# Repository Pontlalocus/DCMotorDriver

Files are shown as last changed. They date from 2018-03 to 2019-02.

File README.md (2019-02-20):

# Project:  BJT HS DC Motor Driver

## DCMotorDriver
DC Motor Driver Simple Board using Bipolar Junction Transistor (BJT).

# 1.0  Glosary

**BJT** - Bipolar Junction Transistor

**DC** - Direct Current

**Qty**  - Quantity

**Mon** - Monitor

**PCB** - Printed Circuit Board

**Ref Des** - Reference Designator

## 2.0  Overview

DC Motor Driver board is a shield for Arduino nano to drive motors on the simplest way possible.   It uses only high side driver suply to the motor with Bipolar Junction Transistors (BJT).

The Board can handle 4 Motors each of the motors are connected to the V(+) and V(-) directly to the output.  No other connections to drive th motors are required.

This board will only operate as a high side driver with 4 oputputs that can handle PWM pulses.  The PWM pulses are internally generated on the Arduino nano.   It is important that the Arduino nano is assembled to the board and programmed with the correct software for the motors to be able to work.

The board is capable of reading the current of each motor independently by using a shunt resistor to ground.   The current measurement is injected to the Analaog port of the Arduino Nano.   We use the Ports A0 to A3 to each of the motor current.  More information on how to read the values is explained below.

## 3.0  Block Diagram

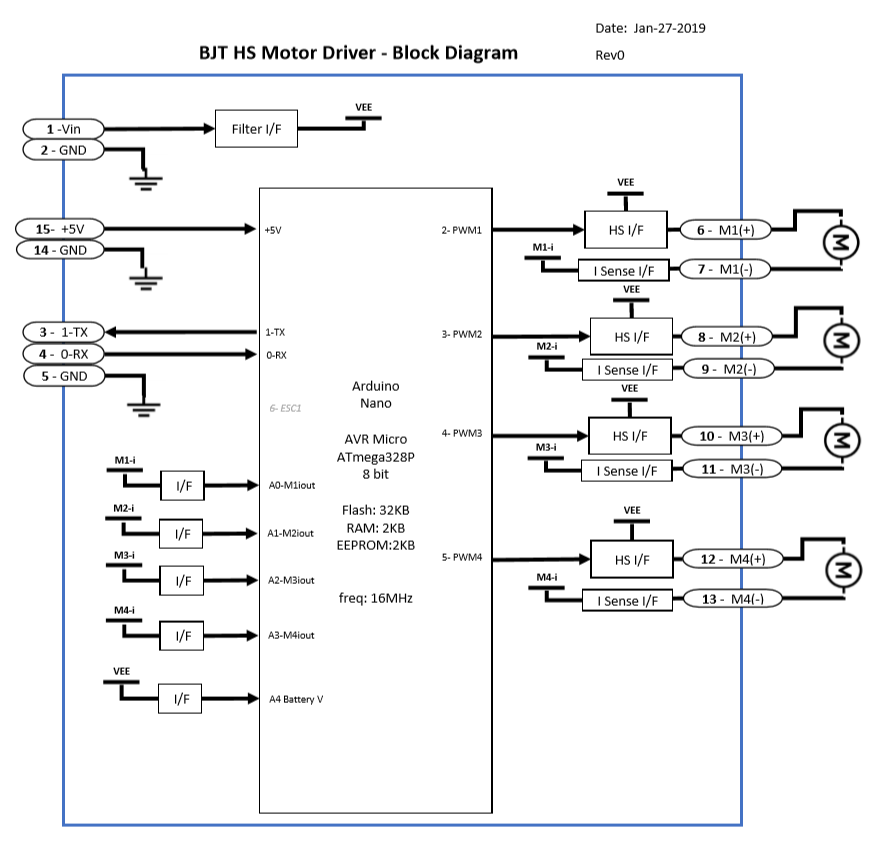
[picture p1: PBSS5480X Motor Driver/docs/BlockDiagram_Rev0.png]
BJT DC Motor Driver Block Diagram


## 4.0  External Connections   

## 4.1  Main Connector Pinout

|  Ref Des | Pin # | Signal Name | Description |
| --- |---| ---|---|
| P7 | 1 | Vin |  Power Battery |
| P7 | 2 | GND |  Ground |
| P7 | 3 | 1-TX |  Serial TX |
| P7 | 4 | 0-RX |  Serial RX |
| P7 | 5 | GND |  Ground |
| P7 | 6 | Motor1-V+ |  Motor1(+) |
| P7 | 7 | Motor1-V- |  Motor1(-) |
| P7 | 8 | Motor2-V+ |  Motor2(+) |
| P7 | 9 | Motor2-V- |  Motor2(-) |
| P7 | 10 | Motor3-V+ |  Motor3(+) |
| P7 | 11 | Motor3-V- |  Motor3(-) |
| P7 | 12 | Motor4-V+ |  Motor4(+) |
| P7 | 13 | Motor4-V- |  Motor4(-) |
| P7 | 14 | GND |  Ground |
| P7 | 15 | +5V |  Power +5V |

## 4.2  Arduino Nano Connector

|  Ref Des | Pin # | Signal Name | Description |
| --- |---| ---|---|
| P1 | 1 | 1-TX |  Serial TX |
| P1 | 2 | 0-RX |  Serial RX |
| P1 | 3 | Reset |  Reset |
| P1 | 4 | GND |  Ground |
| P1 | 5 | 2-PWM1 |  Motor1 - PWM1 |
| P1 | 6 | 3-PWM2 |  Motor2 - PWM2 |
| P1 | 7 | 4-PWM3 |  Motor3 - PWM3 |
| P1 | 8 | 5-PWM4 |  Motor4 - PWM4 |
| P1 | 9 | 6-ESC1 |  Reserved |
| P1 | 10 | Not Used |  Not Used |
| P1 | 11 | Not Used |  Not Used |
| P1 | 12 | Not Used |  Not Used |
| P1 | 13 | Not Used |  Not Used |
| P1 | 14 | Not Used |  Not Used |
| P1 | 15 | Not Used |  Not Used |
| P2 | 1 | Vin |  Power Battery |
| P2 | 2 | GND |  Ground |
| P2 | 3 | Reset |  Reset |
| P2 | 4 | +5V |  Power +5V |
| P2 | 5 | Not Used |  Not Used |
| P2 | 6 | Not Used |  Not Used |
| P2 | 7 | Not Used |  Not Used |
| P2 | 8 | A4 - Battery_V |  Battery Voltage IN |
| P2 | 9 | A3 - Motor4_iout | Motor 4 current Mon |
| P2 | 10 | A2 - Motor3_iout | Motor 3 current Mon |
| P2 | 11 | A1 - Motor2_iout | Motor 2 current Mon |
| P2 | 12 | A0 -  Motor2_iout| Motor 1 current Mon |
| P2 | 13 | AREF | Not Used |
| P2 | 14 | +3.3V | Power 3.3V |
| P2 | 15 | 13 - SCK | Serial Clock |

## 5.0  General Specifications

General Specifications include typical operation specifications

## 5.1  Typical Specifications

**Operation Voltage**: Battery Vin must be equal to 9V +/- 1V
**Operating Temperature**: 0°C to 40°C
**Battery Input Current**:
1.  No Load = <_Pending_>.
2.  Individual Motor Max Load =<_xx A_>.
3.  All Motors Max Load = <_xx A_>.

**Battery Voltage Monitor Range**:  VBAT * 0.5.

**Battery Monitor Low Pass Filter**: <_Pending_>.

**Motor Current Monitor Formula**: Current * 0.1 in Amps.

**Motor Current Low Pass Filter**: <_Pending_>.

_Note: Motor current is same formula for all motors: Motor1, Motor2, Motor3 and Motor4

##  Project Design

## 6.1  Schematic Diagram

Refer to Schematic Diagram for wiring connections of the Project

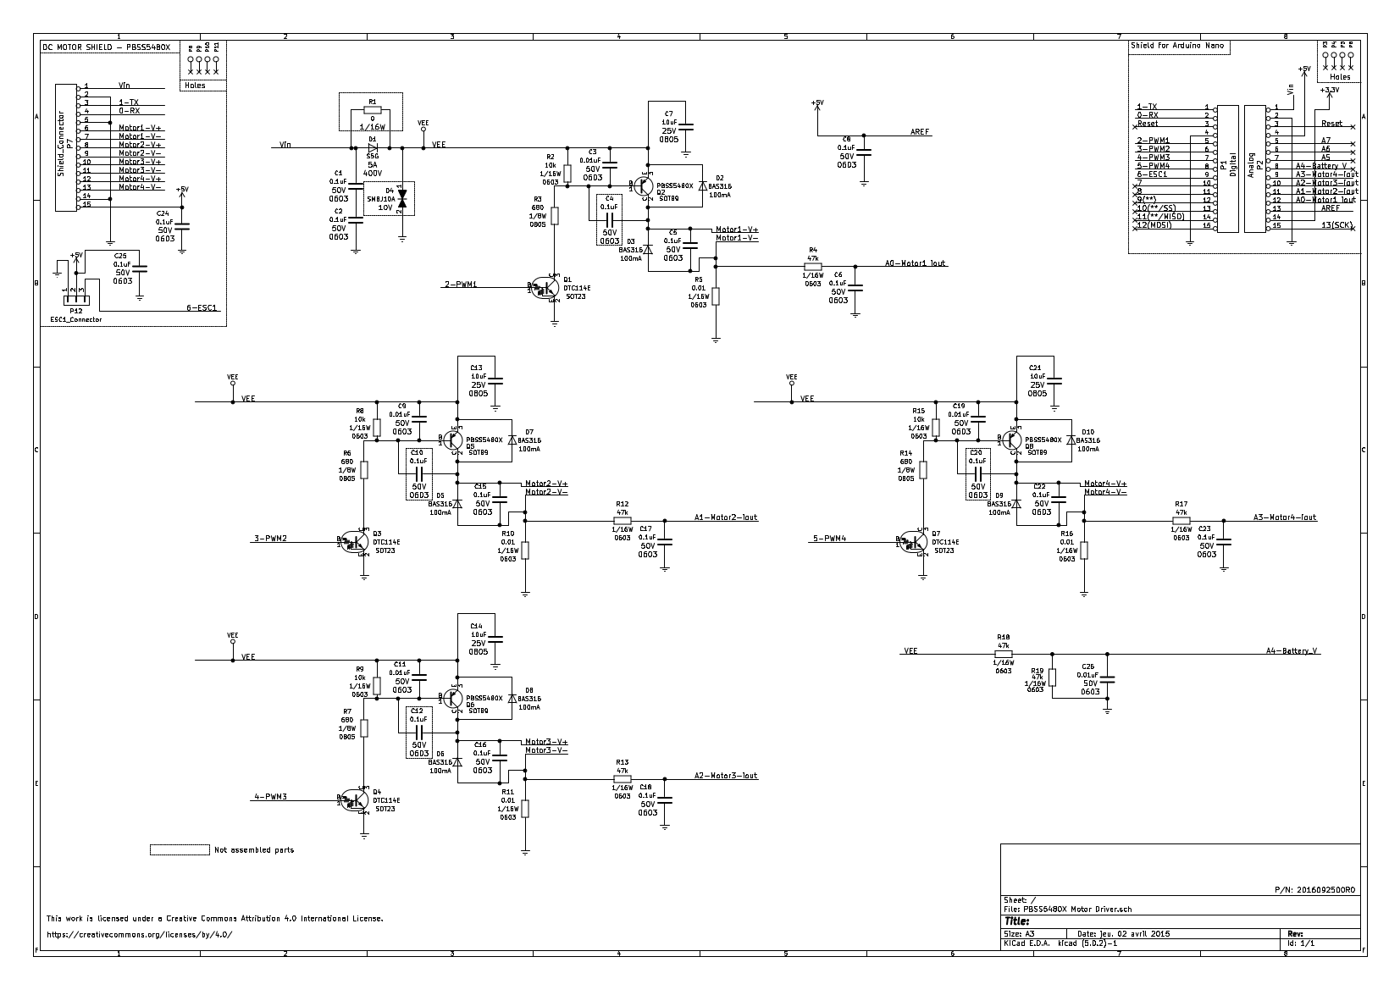
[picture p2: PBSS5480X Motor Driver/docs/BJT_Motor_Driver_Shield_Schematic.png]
Schematic Diagram


This project requires the Arduino Nano board to be used.  For information on the schematic diagram of the Arduino Nano please refer to the following page

Arduino Nano Schematic Diagram

Note: External Link

## 6.2 Bill of Material

The following list of components are selected for the Design.  All are discrete components:

|  Item # | Description | Qty | Reference Designator |
| --- |---| ----|---|
| 1 | PCB bare boards FR-4 Tg=140 2L | 1 |  PCB 1 |
| 2 | DIODE GEN PURP 250V 200MA SOD323 | 8 |  D2 D3 D7 D5 D8 D6 D9 D10 |
| 3 | CAP CER 10000PF 50V X7R 0603 | 5 |  C3 C9 C11 C19 C26 |
| 4 | CAP CER 0.1UF 50V X7R 0603 | 17  |  C6 C8 C17 C18 C23 C1 C2 C5 C15 C16 C22 C24 C25 |
| 5 | CAP CER 10UF 16V X7R 0805 | 4 |  C7 C13 C14 C21 |
| 6 | TRANS PNP 80V 4A SOT89 | 4 |  Q2 Q5 Q6 Q8 |
| 7 | TRANS PREBIAS NPN 246MW SOT23-3  | 4 |  Q1 Q3 Q4 Q7 |
| 8 | RES 0.01 OHM 1% 1/4W 0603 | 4 |  R5 R10 R11 R16 |
| 9 | RES SMD 10K OHM 5% 1/10W 0603 | 4 |  R2 R8 R9 R15 |
| 10 | RES SMD 47K OHM 5% 1/10W 0603 | 6 |  R4 R12 R13 R17 R18 R19 |
| 11 | RES SMD 0 OHM JUMPER 1/10W 0603  | 0 | |
| 12 | RES SMD 680 OHM 1% 1/8W 0805 | 4 |  R3 R6 R7 R14 |
| 13 | DIODE GEN PURP 400V 5A DO214AB | 1 |  D1 |
| 14 | TVS DIODE 10V 17V DO214AA | 1 |  D4 |
| 15 | Arduino Nano Board | 1 |  BOARD 1 |

The following list are components that are not assembled in the board

### Not Assembled 
C4 C10 C12 C20 R1

## 6.3  PCB Specification

PCB Board is FR-4.  Tickness 1.6mm.  2 layers.  Top Side Assembly.  Silkscreen in Top Side only.

Supplier selected for the first Job is JLPCB

### 6.3.1 PCB Design Top View 

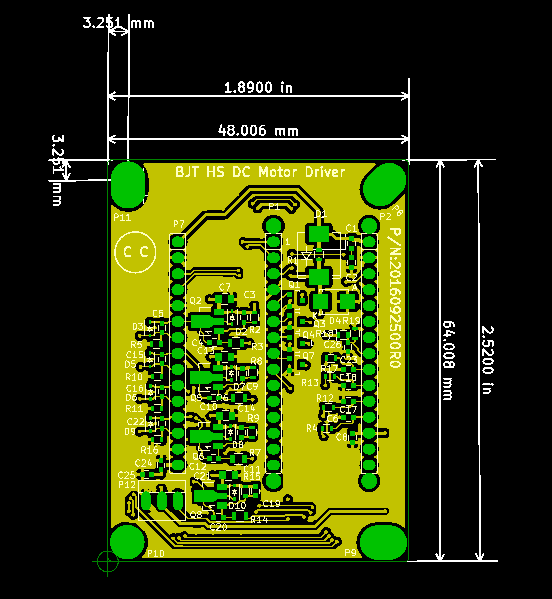
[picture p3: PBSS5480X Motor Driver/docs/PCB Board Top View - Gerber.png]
PCB Top View


### 6.3.2 PCB Design Bottom View

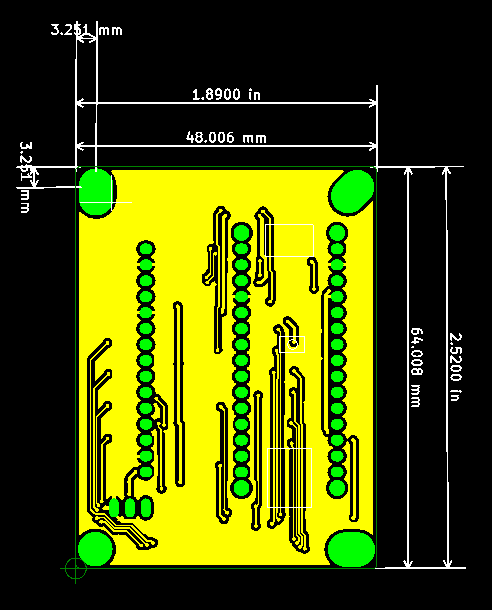
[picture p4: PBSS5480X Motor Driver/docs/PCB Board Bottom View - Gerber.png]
PCB Bottom View


##  7.0  Design Verification

For making sure the board functioanlity is working correctly the following Components are used.  Follow the connection diagram and test the functioanlity of the board with this Software

## 7.1  External Components Requirements

Required External Components

### 7.1.1  Power Pack

Power Pack: 9V
Example:
<_Pending_>.

### 7.1.2  DC Voltage Regulator

DC Voltage Regulator 5V
Example:
<_Pending_>.

### 7.1.3  DC Motor

2.  DC Motor: 
Example:
<_Pending_>.

## 7.2  Design Verification Connections

Todo:  Add connections to system with actual pictures

## 7.3  Design Verification Software

Todo:  Software components,  How does the software works, how to flash software,  how to run software, 

## 7.4  Measure of the output signals and confirmation of General Specifications

Todo:  use a measurement device to confirm General Specifications:  Supply Voltage, Actual current vs adruino measured x 4, PWM signal x 4, Battery Monitor. 

## 8.0  Future Generation Improvements

### 8.1 TODO
1.  Add MQTT RF Transmitter
2.  Add Sensors for 3 axis accelerometer, Gyroscpe and Compass
3.  Add Output for Servo

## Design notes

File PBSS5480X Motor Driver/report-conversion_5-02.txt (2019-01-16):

Info: Backing up file “C:\Users\eduar\OneDrive\Documents\Github\DCMotorDriver\PBSS5480X Motor Driver\sym-lib-table” to file “C:\Users\eduar\OneDrive\Documents\Github\DCMotorDriver\PBSS5480X Motor Driver\rescue-backup\sym-lib-table-2019-01-15-23-58-39”.
Info: Backing up file “C:\Users\eduar\OneDrive\Documents\Github\DCMotorDriver\PBSS5480X Motor Driver\PBSS5480X Motor Driver.sch” to file “C:\Users\eduar\OneDrive\Documents\Github\DCMotorDriver\PBSS5480X Motor Driver\rescue-backup\PBSS5480X Motor Driver-2019-01-15-23-58-39.sch”.
Info: Backing up file “C:\Users\eduar\OneDrive\Documents\Github\DCMotorDriver\PBSS5480X Motor Driver\PBSS5480X Motor Driver.pro” to file “C:\Users\eduar\OneDrive\Documents\Github\DCMotorDriver\PBSS5480X Motor Driver\rescue-backup\PBSS5480X Motor Driver-2019-01-15-23-58-39.pro”.
Info: Backing up file “C:\Users\eduar\OneDrive\Documents\Github\DCMotorDriver\PBSS5480X Motor Driver\PBSS5480X Motor Driver-cache.lib” to file “C:\Users\eduar\OneDrive\Documents\Github\DCMotorDriver\PBSS5480X Motor Driver\rescue-backup\PBSS5480X Motor Driver-cache-2019-01-15-23-58-39.lib”.
Info: Backing up file “C:\Users\eduar\OneDrive\Documents\Github\DCMotorDriver\PBSS5480X Motor Driver\PBSS5480X Motor Driver-rescue.lib” to file “C:\Users\eduar\OneDrive\Documents\Github\DCMotorDriver\PBSS5480X Motor Driver\rescue-backup\PBSS5480X Motor Driver-rescue-2019-01-15-23-58-39.lib”.
Info: Backing up file “C:\Users\eduar\OneDrive\Documents\Github\DCMotorDriver\PBSS5480X Motor Driver\PBSS5480X Motor Driver-rescue.dcm” to file “C:\Users\eduar\OneDrive\Documents\Github\DCMotorDriver\PBSS5480X Motor Driver\rescue-backup\PBSS5480X Motor Driver-rescue-2019-01-15-23-58-39.dcm”.
Info: Adding library “PBSS5480X-Motor-Driver-rescue”, file “${KIPRJMOD}/PBSS5480X Motor Driver-rescue.lib” to project symbol library table.
Symbol “CONN_1” mapped to symbol library “PBSS5480X-Motor-Driver-rescue”.
Symbol “CONN_1” mapped to symbol library “PBSS5480X-Motor-Driver-rescue”.
Symbol “CONN_1” mapped to symbol library “PBSS5480X-Motor-Driver-rescue”.
Symbol “CONN_1” mapped to symbol library “PBSS5480X-Motor-Driver-rescue”.
Symbol “CONN_15” mapped to symbol library “PBSS5480X-Motor-Driver-rescue”.
Symbol “CONN_15” mapped to symbol library “PBSS5480X-Motor-Driver-rescue”.
Symbol “DTC114E” mapped to symbol library “PBSS5480X-Motor-Driver-rescue”.
Symbol “BCX53” mapped to symbol library “PBSS5480X-Motor-Driver-rescue”.
Symbol “R” mapped to symbol library “Device”.
Symbol “D” mapped to symbol library “Device”.
Symbol “D” mapped to symbol library “Device”.
Symbol “R” mapped to symbol library “Device”.
Symbol “GNDREF” mapped to symbol library “power”.
Symbol “C” mapped to symbol library “Device”.
Symbol “C” mapped to symbol library “Device”.
Symbol “GNDREF” mapped to symbol library “power”.
Symbol “GNDREF” mapped to symbol library “power”.
Symbol “R” mapped to symbol library “Device”.
Symbol “C” mapped to symbol library “Device”.
Symbol “C” mapped to symbol library “Device”.
Symbol “C” mapped to symbol library “Device”.
Symbol “R” mapped to symbol library “Device”.
Symbol “C” mapped to symbol library “Device”.
Symbol “TVS” mapped to symbol library “PBSS5480X-Motor-Driver-rescue”.
Symbol “GNDREF” mapped to symbol library “power”.
Symbol “C” mapped to symbol library “Device”.
Symbol “GNDREF” mapped to symbol library “power”.
Symbol “R” mapped to symbol library “Device”.
Symbol “C” mapped to symbol library “Device”.
Symbol “GNDREF” mapped to symbol library “power”.
Symbol “+3.3V” mapped to symbol library “power”.
Symbol “GNDREF” mapped to symbol library “power”.
Symbol “GNDREF” mapped to symbol library “power”.
Symbol “VEE” mapped to symbol library “power”.
Symbol “GNDREF” mapped to symbol library “power”.
Symbol “DTC114E” mapped to symbol library “PBSS5480X-Motor-Driver-rescue”.
Symbol “BCX53” mapped to symbol library “PBSS5480X-Motor-Driver-rescue”.
Symbol “R” mapped to symbol library “Device”.
Symbol “GNDREF” mapped to symbol library “power”.
Symbol “GNDREF” mapped to symbol library “power”.
Symbol “R” mapped to symbol library “Device”.
Symbol “C” mapped to symbol library “Device”.
Symbol “C” mapped to symbol library “Device”.
Symbol “C” mapped to symbol library “Device”.
Symbol “R” mapped to symbol library “Device”.
Symbol “C” mapped to symbol library “Device”.
Symbol “C” mapped to symbol library “Device”.
Symbol “GNDREF” mapped to symbol library “power”.
Symbol “R” mapped to symbol library “Device”.
Symbol “VEE” mapped to symbol library “power”.
Symbol “GNDREF” mapped to symbol library “power”.
Symbol “DTC114E” mapped to symbol library “PBSS5480X-Motor-Driver-rescue”.
Symbol “BCX53” mapped to symbol library “PBSS5480X-Motor-Driver-rescue”.
Symbol “R” mapped to symbol library “Device”.
Symbol “GNDREF” mapped to symbol library “power”.
Symbol “GNDREF” mapped to symbol library “power”.
Symbol “R” mapped to symbol library “Device”.
Symbol “C” mapped to symbol library “Device”.
Symbol “C” mapped to symbol library “Device”.
Symbol “C” mapped to symbol library “Device”.
Symbol “R” mapped to symbol library “Device”.
Symbol “C” mapped to symbol library “Device”.
Symbol “C” mapped to symbol library “Device”.
Symbol “GNDREF” mapped to symbol library “power”.
Symbol “R” mapped to symbol library “Device”.
Symbol “VEE” mapped to symbol library “power”.
Symbol “DTC114E” mapped to symbol library “PBSS5480X-Motor-Driver-rescue”.
Symbol “BCX53” mapped to symbol library “PBSS5480X-Motor-Driver-rescue”.
Symbol “R” mapped to symbol library “Device”.
Symbol “GNDREF” mapped to symbol library “power”.
Symbol “GNDREF” mapped to symbol library “power”.
Symbol “R” mapped to symbol library “Device”.
Symbol “C” mapped to symbol library “Device”.
Symbol “C” mapped to symbol library “Device”.
Symbol “C” mapped to symbol library “Device”.
Symbol “R” mapped to symbol library “Device”.
Symbol “C” mapped to symbol library “Device”.
Symbol “C” mapped to symbol library “Device”.
Symbol “GNDREF” mapped to symbol library “power”.
Symbol “R” mapped to symbol library “Device”.
Symbol “VEE” mapped to symbol library “power”.
Symbol “GNDREF” mapped to symbol library “power”.
Symbol “CONN_15” mapped to symbol library “PBSS5480X-Motor-Driver-rescue”.
Symbol “GNDREF” mapped to symbol library “power”.
Symbol “+5V” mapped to symbol library “power”.
Symbol “+5V” mapped to symbol library “power”.
Symbol “CONN_1” mapped to symbol library “PBSS5480X-Motor-Driver-rescue”.
Symbol “CONN_1” mapped to symbol library “PBSS5480X-Motor-Driver-rescue”.
Symbol “CONN_1” mapped to symbol library “PBSS5480X-Motor-Driver-rescue”.
Symbol “CONN_1” mapped to symbol library “PBSS5480X-Motor-Driver-rescue”.
Symbol “+5V” mapped to symbol library “power”.
Symbol “C” mapped to symbol library “Device”.
Symbol “GNDREF” mapped to symbol library “power”.
Symbol “GNDREF” mapped to symbol library “power”.
Symbol “D” mapped to symbol library “Device”.
Symbol “D” mapped to symbol library “Device”.
Symbol “D” mapped to symbol library “Device”.
Symbol “D” mapped to symbol library “Device”.
Symbol “D” mapped to symbol library “Device”.
Symbol “D” mapped to symbol library “Device”.
Symbol “D” mapped to symbol library “Device”.
Symbol “CONN_01X03” mapped to symbol library “PBSS5480X-Motor-Driver-rescue”.
Symbol “GNDREF” mapped to symbol library “power”.
Symbol “+5V” mapped to symbol library “power”.
Symbol “C” mapped to symbol library “Device”.
Symbol “GNDREF” mapped to symbol library “power”.
Symbol “R” mapped to symbol library “Device”.
Symbol “C” mapped to symbol library “Device”.
Symbol “R” mapped to symbol library “Device”.
Symbol “GNDREF” mapped to symbol library “power”.
Info: Symbol library table mapping complete!

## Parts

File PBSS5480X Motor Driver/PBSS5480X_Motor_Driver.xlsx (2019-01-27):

Item | Description | Mfr | MfrPN | Mfr1 | MfrPN1 | Quantity | Reference Designator | Digikey PO Qty | Digikey PO cost | Rating | Case | Footprint | Link
1 | PCB bare boards FR-4 Tg=140 2L | JLCPCB | Y2-2385543A |  |  | 1 | 1 | 10 | 20.46
2 | DIODE GEN PURP 250V 200MA SOD323 | NXP | BAS316,115 | On Semiconductor | BAS21HT1G | 8 | D2 D3 D7 D5 D8 D6 D9 D10 | 100 | 9.56 |  | SOD-323 | Diodes_SMD:SOD-323 | http://www.digikey.com/product-detail/en/nxp-semiconductors/BAS316,115/568-5003-2-ND/1232076
3 | CAP CER 10000PF 50V X7R 0603 | Murata | GRM188R71H103KA01D |  |  | 5 | C3 C9 C11 C19 C26 | 100 | 2.89 | 50V | 603 | Capacitors_SMD:C_0603 | http://www.digikey.com/product-detail/en/murata-electronics-north-america/GRM188R71H103KA01D/490-1512-2-ND/587151
4 | CAP CER 0.1UF 50V X7R 0603 | Murata | GRM188R71H104KA93D | KEMET | C0603C104M5RACTU | 17 | C6 C8 C17 C18 C23 C1 C2 C5 C4 C15 C10 C16 C12 C22 C20 C24 C25 | 200 | 3.1 | 50V | 603 | Capacitors_SMD:C_0603
5 | CAP CER 10UF 16V X7R 0805 | Murata | GRM21BR71A106KA73L | Taiyo Yuden | EMK212BB7106MG-T | 4 | C7 C13 C14 C21 | 50 | 19.95 | 16V | 805 | Capacitors_SMD:C_0805 | http://www.digikey.com/product-detail/en/murata-electronics-north-america/GRM21BR71A106KA73L/490-10516-2-ND/5027600
6 | TRANS PNP 80V 4A SOT89 | NXP | PBSS5480X,135 | Nexperia | PBSS5540X,135 | 4 | Q2 Q5 Q6 Q8 | 100 | 27.8 |  | SOT89 | TO_SOT_Packages_SMD:SOT89-3_Housing
7 | TRANS PREBIAS NPN 246MW SOT23-3 | NXP | PDTC114ET,215 | On Semiconductor | MMUN2211LT3G | 4 | Q1 Q3 Q4 Q7 | 100 | 6.42 |  | SOT23 | TO_SOT_Packages_SMD:SOT-23
8 | RES 0.01 OHM 1% 1/4W 0603 | Yageo | PE0603DRF070R01L | Panasonic | ERJ-3LWFR010V | 4 | R5 R10 R11 R16 | 100 | 17.12 | 1/16W | 603 | Resistors_SMD:R_0603
9 | RES SMD 10K OHM 5% 1/10W 0603 | Yageo | RC0603FR-0710KL | Panasonic | ERJ-3GEYJ103V | 4 | R2 R8 R9 R15 | 100 | 1.92 | 1/16W | 603 | Resistors_SMD:R_0603
10 | RES SMD 47K OHM 5% 1/10W 0603 | Yageo | RC0603FR-0747KL | Panasonic | ERJ-3GEYJ473V | 6 | R4 R12 R13 R17 R18 R19 | 100 | 1.69 | 1/16W | 603 | Resistors_SMD:R_0603
11 | RES SMD 0 OHM JUMPER 1/10W 0603 | Yageo | RC0603JR-070RL |  |  | 1 | R1 | 100 | 0.77 | 1/16W |  | Resistors_SMD:R_0603
12 | RES SMD 680 OHM 1% 1/8W 0805 | Yageo | RC0805FR-07680RL |  |  | 4 | R3 R6 R7 R14 | 100 | 1.69 | 1/8W | 805 | Resistors_SMD:R_0805
13 | DIODE GEN PURP 400V 5A DO214AB | Vishay | S5G-E3/57T |  |  | 1 | D1 | 10 | 4.05 |  |  | Diodes_SMD:SMC_Standard
14 | TVS DIODE 10V 17V DO214AA | Vishay | SMBJ10A-E3/52 |  |  | 1 | D4 | 10 | 2.96 |  | SMB | Diodes_SMD:SMB_Standard
15 | Arduino Nano Board | Arduino | A000005 |  |  | 1 | P1 | 10 | 220 |  |  | Connect:Socket_Strip_Arduino_1x15
 |  |  |  |  |  |  |  | Digikey Shipment | 8.99
 |  |  |  |  |  |  |  | Digikey Tax | 6
 |  |  |  |  |  |  |  |  | 355.37
 |  |  |  |  |  |  |  | Unit Cost | 35.537

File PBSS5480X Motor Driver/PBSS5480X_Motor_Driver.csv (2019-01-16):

Id | Designator | Package | Quantity | Designation | Supplier and ref
1 | C1,C2,C4,C5,C6,C8,C10,C12,C15,C16,C17,C18,C20,C22,C23,C24,C25 | C_0603 | 17 | 0.1uF
2 | C3,C9,C11,C19,C26 | C_0603 | 5 | 0.01uF
3 | C7,C13,C14,C21 | C_0805 | 4 | 10uF
4 | D1 | SMC_Standard | 1 | S5G
5 | D4 | SMB_Standard | 1 | SMBJ10A
6 | Q1,Q3,Q4,Q7 | SOT-23 | 4 | DTC114E
7 | R1 | R_0603 | 1 | 0
8 | R2,R8,R9,R15 | R_0603 | 4 | 10k
9 | R3,R6,R7,R14 | R_0805 | 4 | 680
10 | R4,R12,R13,R17,R18,R19 | R_0603 | 6 | 47k
11 | R5,R10,R11,R16 | R_0603 | 4 | 0.01
12 | Q2,Q5,Q6,Q8 | SOT89-3_Housing | 4 | PBSS5480X
13 | P7 | Socket_Strip_Arduino_1x15 | 1 | Shield_Connector
14 | D2,D3,D5,D6,D7,D8,D9,D10 | SOD-323 | 8 | BAS316
15 | P1 | Socket_Strip_Arduino_1x15 | 1 | Digital
16 | P2 | Socket_Strip_Arduino_1x15 | 1 | Analog
17 | P3,P4,P5,P6 | 1pin_Nano | 4 | CONN_1
18 | P12 | PINHEAD1-3 | 1 | ESC1_Connector
19 | P8,P9,P11 | 1pin-5.1mmx7mm | 3 | CONN_1
20 | P10 | 1pin-5.1mm | 1 | CONN_1

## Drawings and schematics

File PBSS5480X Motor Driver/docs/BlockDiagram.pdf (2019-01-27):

BJT HS Motor Driver - Block Diagram | Rev0

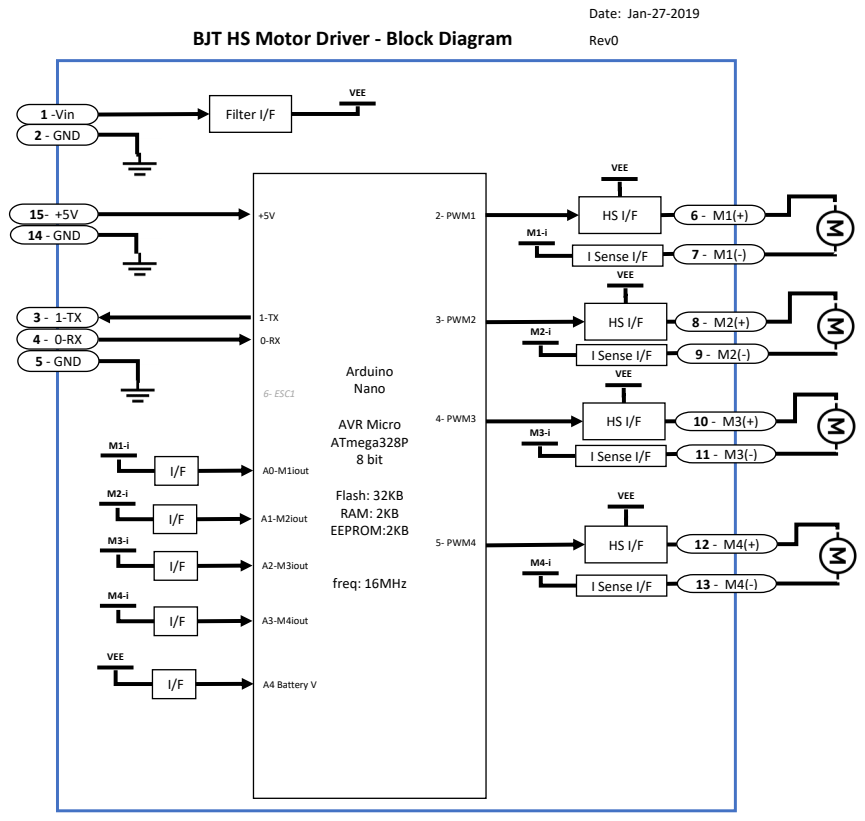
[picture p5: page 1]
Date: Jan-27-2019; Filter I/F; Arduino Nano; AVR Micro ATmega328P 8 bit; Flash: 32KB RAM: 2KB EEPROM:2KB; freq: 16MHz; 2- PWM1; 3- PWM2; 5- PWM4; 6- ESC1; A0-M1iout; A1-M2iout; A2-M3iout; A3-M4iout; 1 -Vin 2 - GND; 3 - 1-TX 4 - 0-RX 5 - GND; 15- +5V 14 - GND; 10 - M3(+) ⁴⁻ PWM3; I Sense I/F; VEE; A4 Battery V

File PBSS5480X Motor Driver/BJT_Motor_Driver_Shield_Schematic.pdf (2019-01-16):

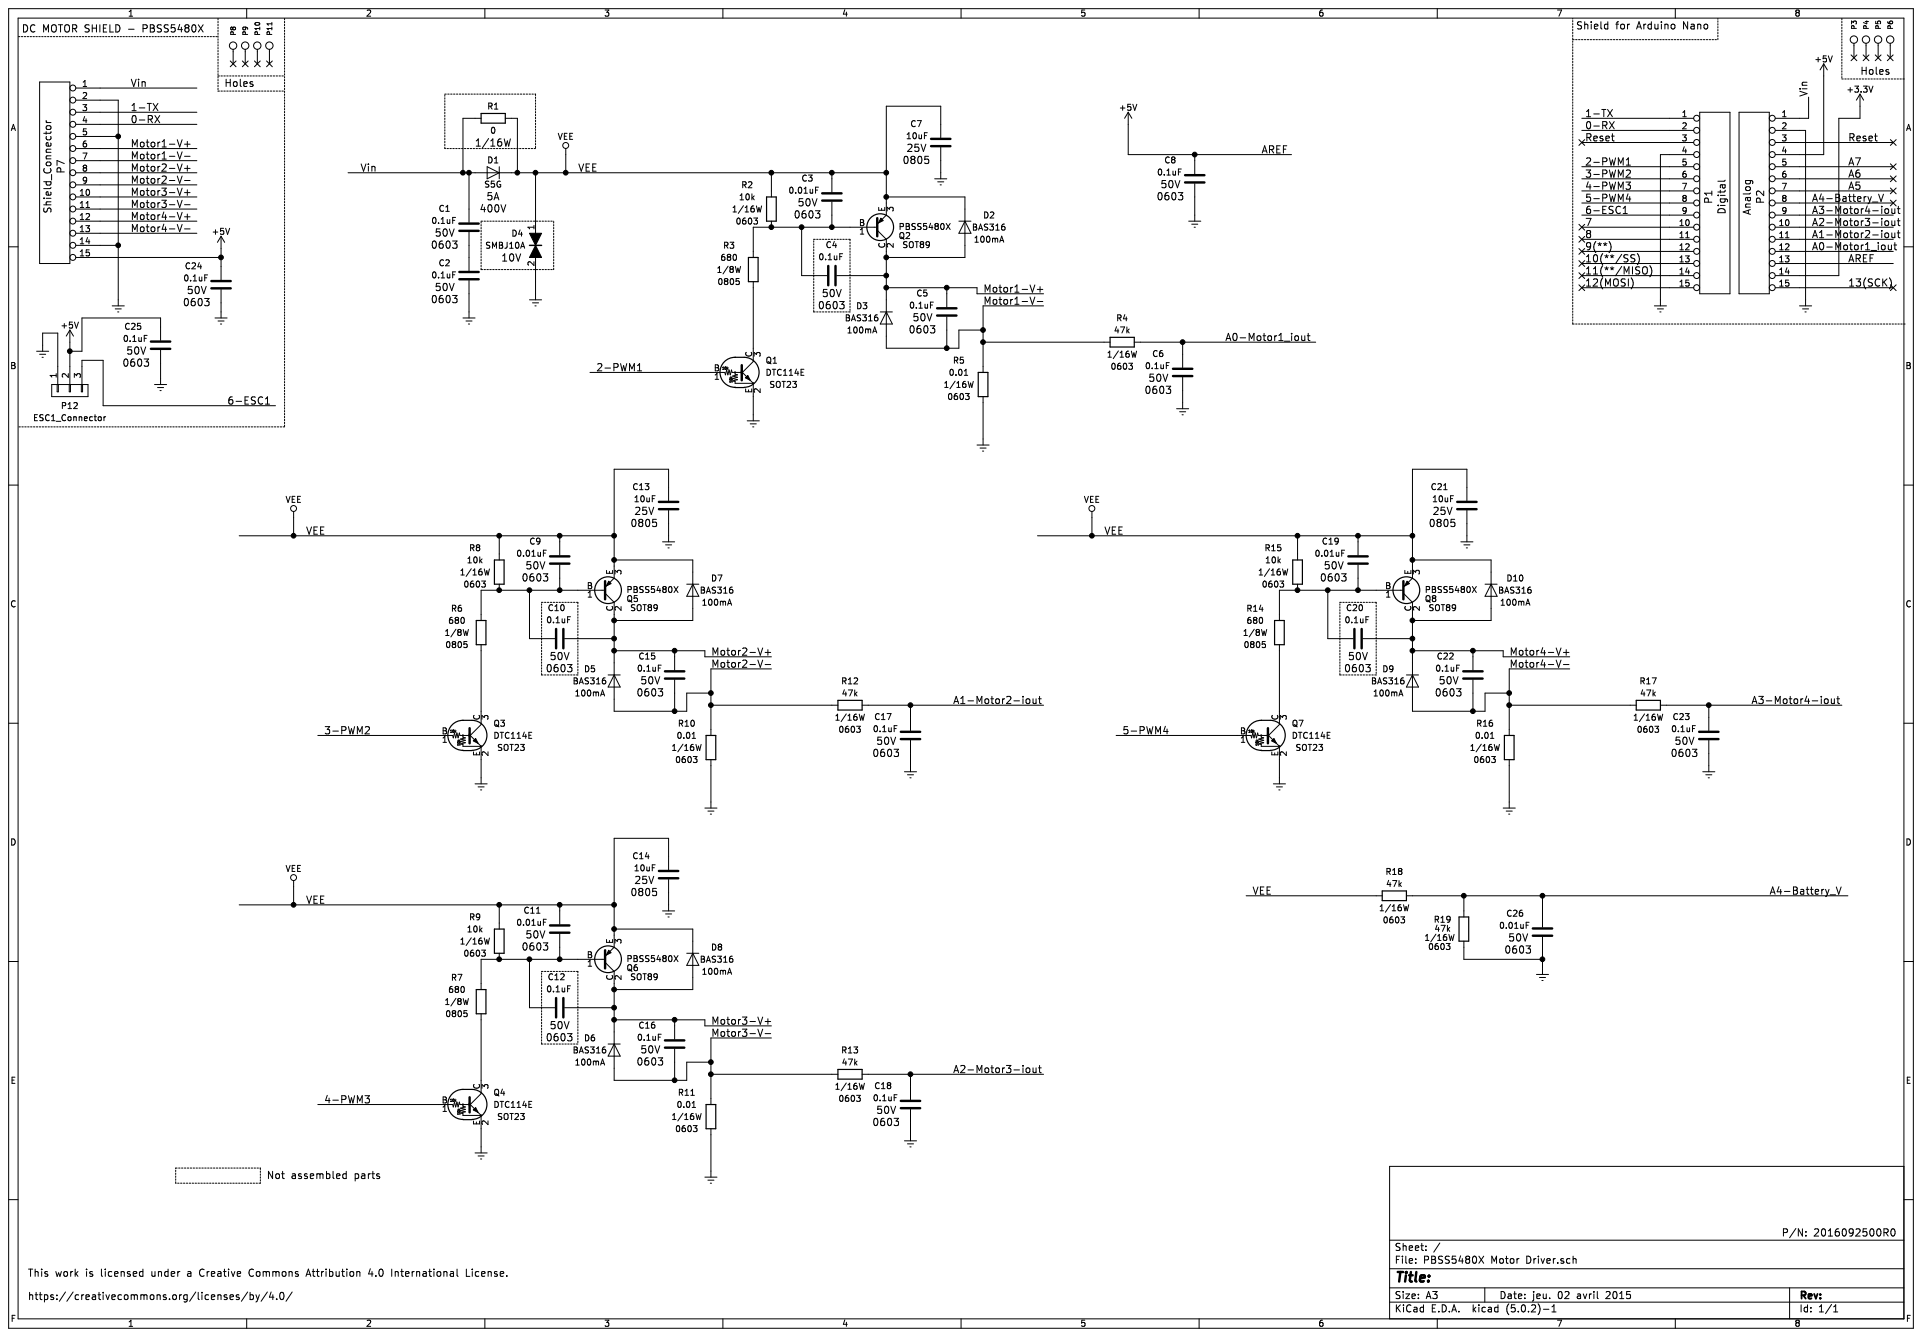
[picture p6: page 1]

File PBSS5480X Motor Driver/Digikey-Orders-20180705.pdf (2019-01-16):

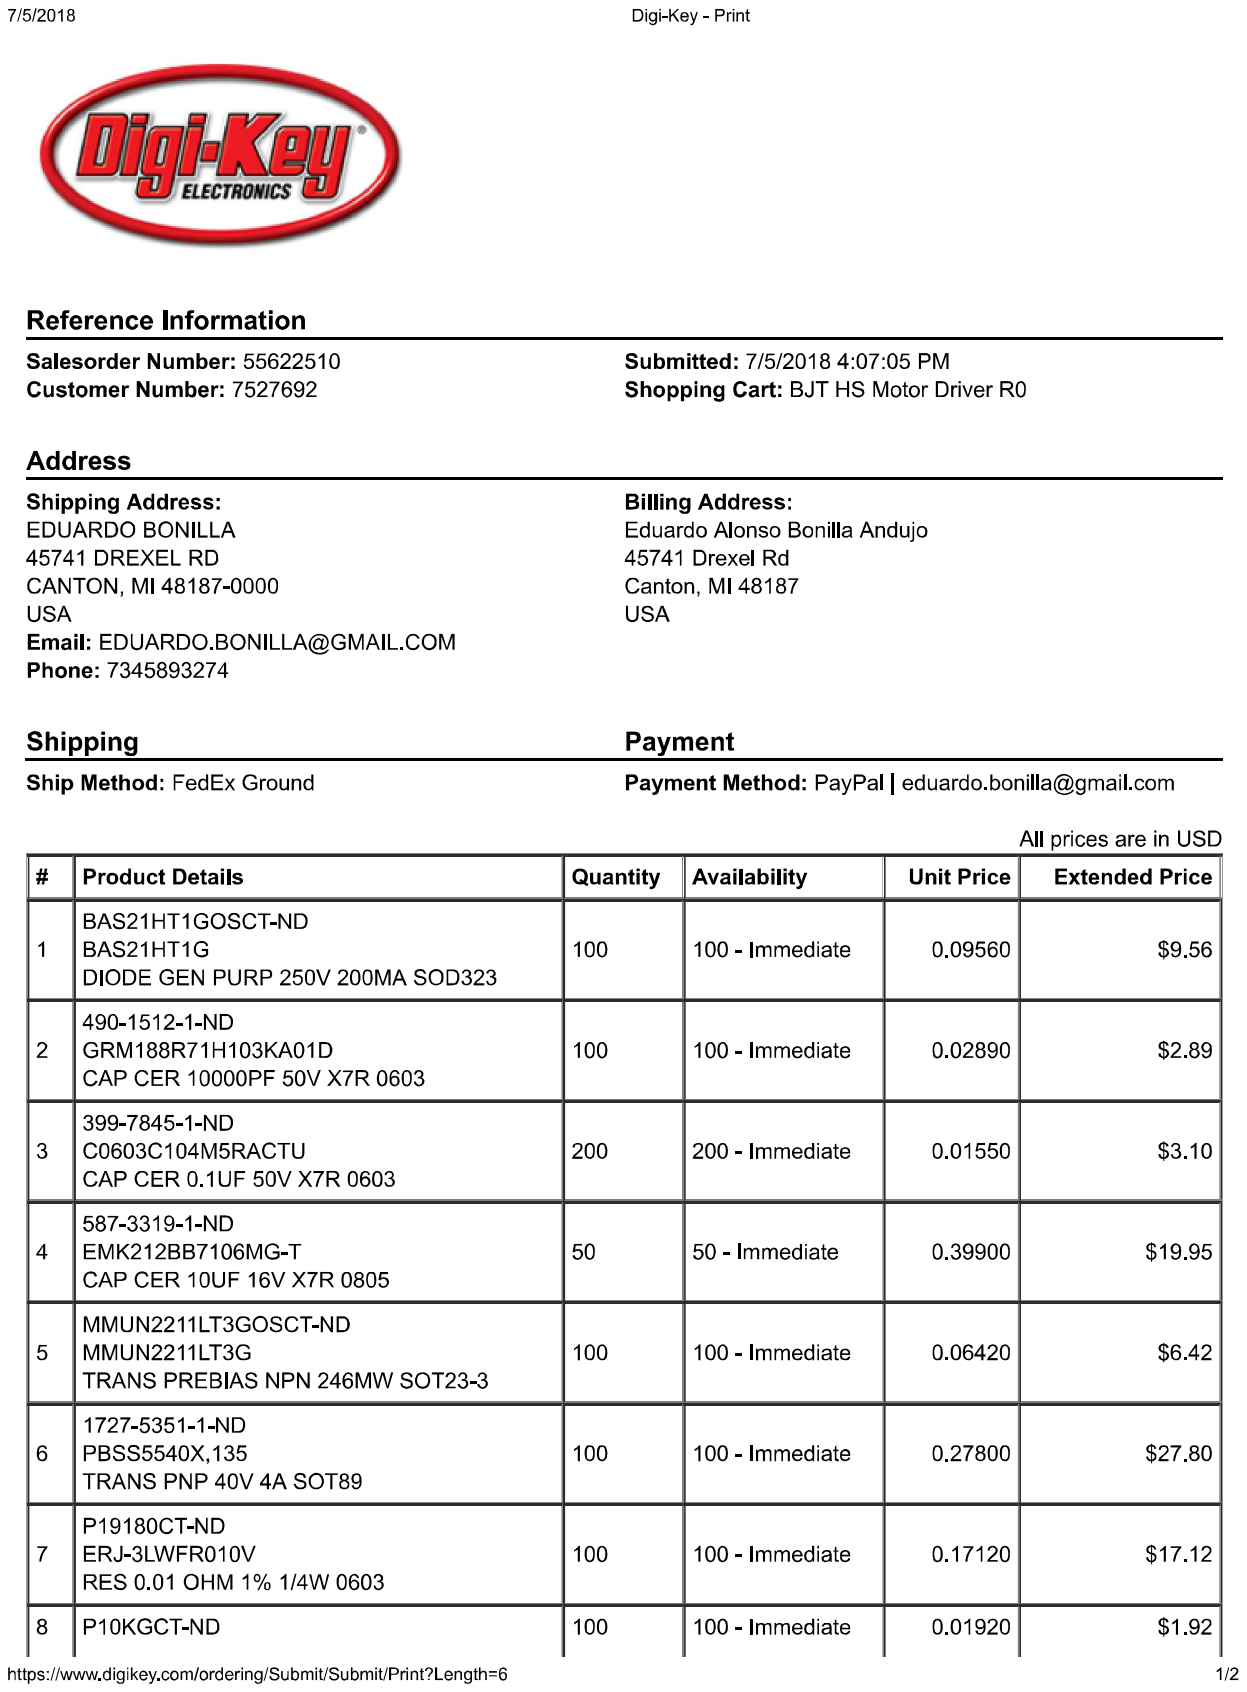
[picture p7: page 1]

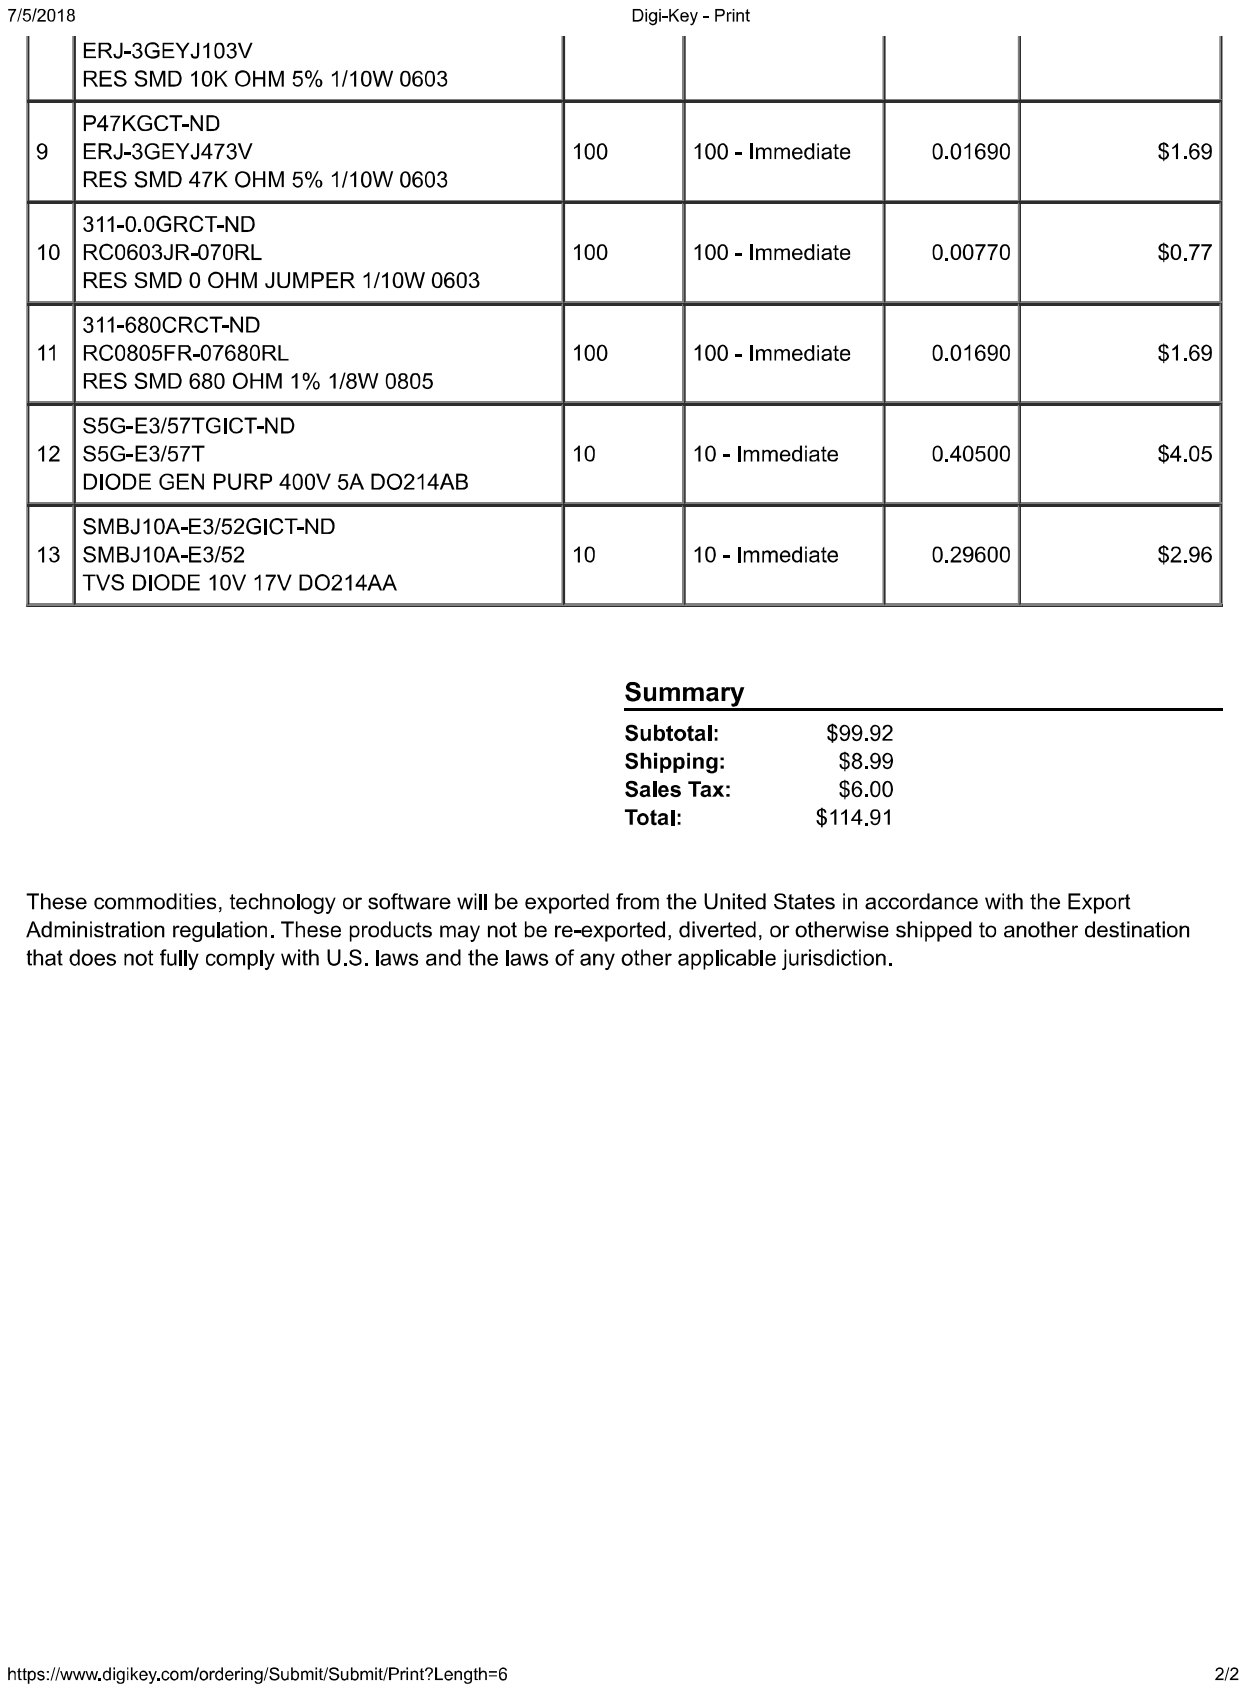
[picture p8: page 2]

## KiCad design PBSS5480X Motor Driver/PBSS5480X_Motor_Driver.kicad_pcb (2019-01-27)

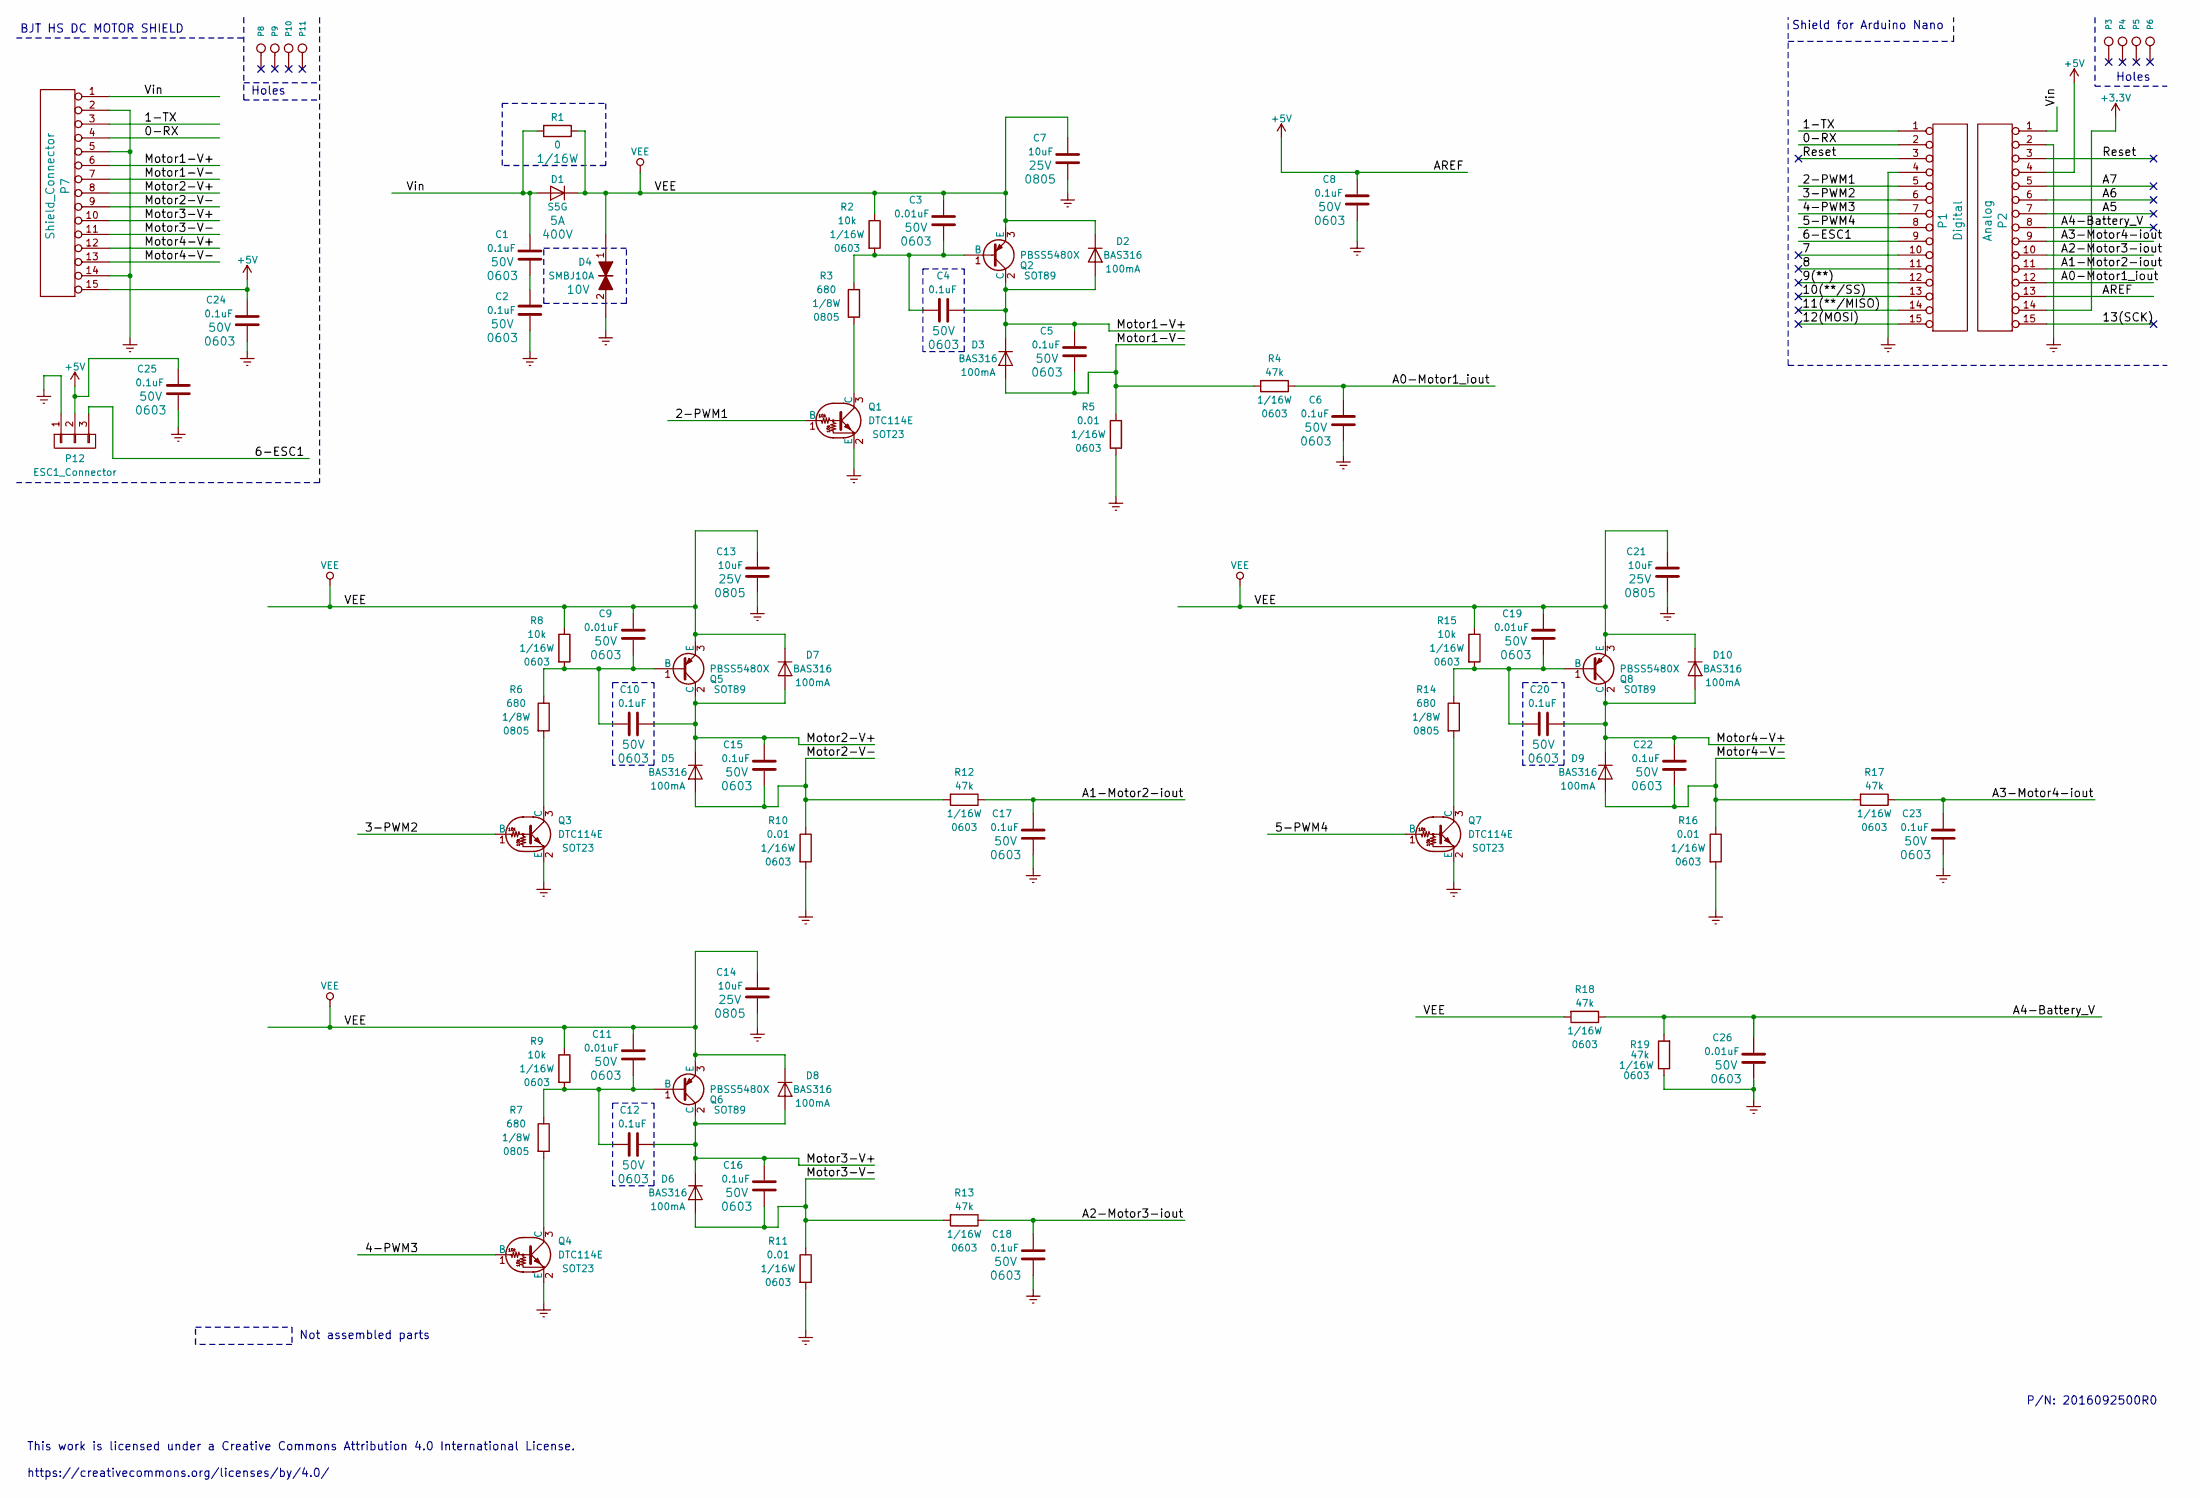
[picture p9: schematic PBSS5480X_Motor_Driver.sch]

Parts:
C1, C2, C4, C5, C6, C8, C10, C12, C15, C16, C17, C18, C20, C22, C23, C24, C25: 0.1uF; C_0603; Rating 50V; MfrPN GRM188R71H104KA93D
C3, C9, C11, C19, C26: 0.01uF; C_0603; Rating 50V; MfrPN GRM188R71H103KA01D
C7, C13, C14, C21: 10uF; C_0805; Rating 25V; MfrPN GRM21BR71A106KA73L
D1: S5G; SMC_Standard; MfrPN S5G-E3/57T
D2, D3, D5, D6, D7, D8, D9, D10: BAS316; SOD-323; MfrPN BAS316,115
D4: SMBJ10A; SMB_Standard; Voltage 10V; MfrPN SMBJ10A-E3/52
P1: Digital; Socket_Strip_Arduino_1x15
P2: Analog; Socket_Strip_Arduino_1x15
P3, P4, P5, P6: CONN_1; 1pin_Nano
P7: Shield_Connector; Socket_Strip_Arduino_1x15
P8, P9, P11: CONN_1; 1pin-5.1mmx7mm
P10: CONN_1; 1pin-5.1mm
P12: ESC1_Connector; PINHEAD1-3
Q1, Q3, Q4, Q7: DTC114E; SOT-23; MfrPN PDTC114ET,215
Q2, Q5, Q6, Q8: PBSS5480X; SOT89-3_Housing; MfrPN PBSS5480X,135
R1: 0; R_0603; Rating 1/16W; MfrPN RC0603JR-070RL
R2, R8, R9, R15: 10k; R_0603; Rating 1/16W; MfrPN RC0603FR-0710KL
R3, R6, R7, R14: 680; R_0805; Rating 1/8W; MfrPN RC0805FR-07680RL
R4, R12, R13, R17, R18, R19: 47k; R_0603; Rating 1/16W; MfrPN RC0603FR-0747KL
R5, R10, R11, R16: 0.01; R_0603; Rating 1/16W; MfrPN PE0603DRF070R01L

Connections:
+3V3: P2.14
+5V: C8.2, C24.2, C25.2, P2.4, P2.13, P7.15 (p15), P12.2
/0-RX: P1.2, P7.4
/1-TX: P1.1, P7.3
/2-PWM1: P1.5, Q1.1 (B)
/3-PWM2: P1.6, Q3.1 (B)
/4-PWM3: P1.7, Q4.1 (B)
/5-PWM4: P1.8, Q7.1 (B)
/6-ESC1: P1.9, P12.3
/7: P1.10
/8: P1.11
/9(**): P1.12
/10(**/SS): P1.13
/11(**/MISO): P1.14
/12(MOSI): P1.15 (p15)
/13(SCK): P2.15 (p15)
/A0-Motor1_iout: C6.2, P2.12, R4.1
/A1-Motor2-iout: C17.2, P2.11, R12.1
/A2-Motor3-iout: C18.2, P2.10, R13.1
/A3-Motor4-iout: C23.2, P2.9, R17.1
/A4-Battery_V: C26.2, P2.8, R18.1, R19.2
/A5: P2.7
/A6: P2.6
/A7: P2.5
/Motor1-V+: C4.2, C5.2, D2.2 (A), D3.1 (K), P7.6, Q2.2 (C)
/Motor1-V-: C5.1, D3.2 (A), P7.7, R4.2, R5.1
/Motor2-V+: C10.2, C15.2, D5.1 (K), D7.2 (A), P7.8, Q5.2 (C)
/Motor2-V-: C15.1, D5.2 (A), P7.9, R10.1, R12.2
/Motor3-V+: C12.2, C16.2, D6.1 (K), D8.2 (A), P7.10, Q6.2 (C)
/Motor3-V-: C16.1, D6.2 (A), P7.11, R11.1, R13.2
/Motor4-V+: C20.2, C22.2, D9.1 (K), D10.2 (A), P7.12, Q8.2 (C)
/Motor4-V-: C22.1, D9.2 (A), P7.13, R16.1, R17.2
/Reset: P1.3, P2.3
/Vin: C1.2, D1.2 (A), P2.1, P7.1, R1.2
GNDREF: C2.1, C6.1, C7.1, C8.1, C13.1, C14.1, C17.1, C18.1, C21.1, C23.1, C24.1, C25.1, C26.1, D4.2, P1.4, P2.2, P7.2, P7.5, P7.14, P12.1, Q1.2 (E), Q3.2 (E), Q4.2 (E), Q7.2 (E), R5.2, R10.2, R11.2, R16.2, R19.1
unnamed: C1.1, C2.2
unnamed: C3.1, C4.1, Q2.1 (B), R2.2, R3.1
unnamed: C9.1, C10.1, Q5.1 (B), R6.1, R8.2
unnamed: C11.1, C12.1, Q6.1 (B), R7.1, R9.2
unnamed: C19.1, C20.1, Q8.1 (B), R14.1, R15.2
unnamed: Q1.3 (C), R3.2
unnamed: Q3.3 (C), R6.2
unnamed: Q4.3 (C), R7.2
unnamed: Q7.3 (C), R14.2
VEE: C3.2, C7.2, C9.2, C11.2, C13.2, C14.2, C19.2, C21.2, D1.1 (K), D2.1 (K), D4.1, D7.1 (K), D8.1 (K), D10.1 (K), Q2.3 (E), Q5.3 (E), Q6.3 (E), Q8.3 (E), R1.1, R2.1, R8.1, R9.1, R15.1, R18.2

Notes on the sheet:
Holes
Shield for Arduino Nano
BJT HS DC MOTOR SHIELD
Not assembled parts
This work is licensed under a Creative Commons Attribution 4.0 International License. https://creativecommons.org/licenses/by/4.0/
P/N: 2016092500R0

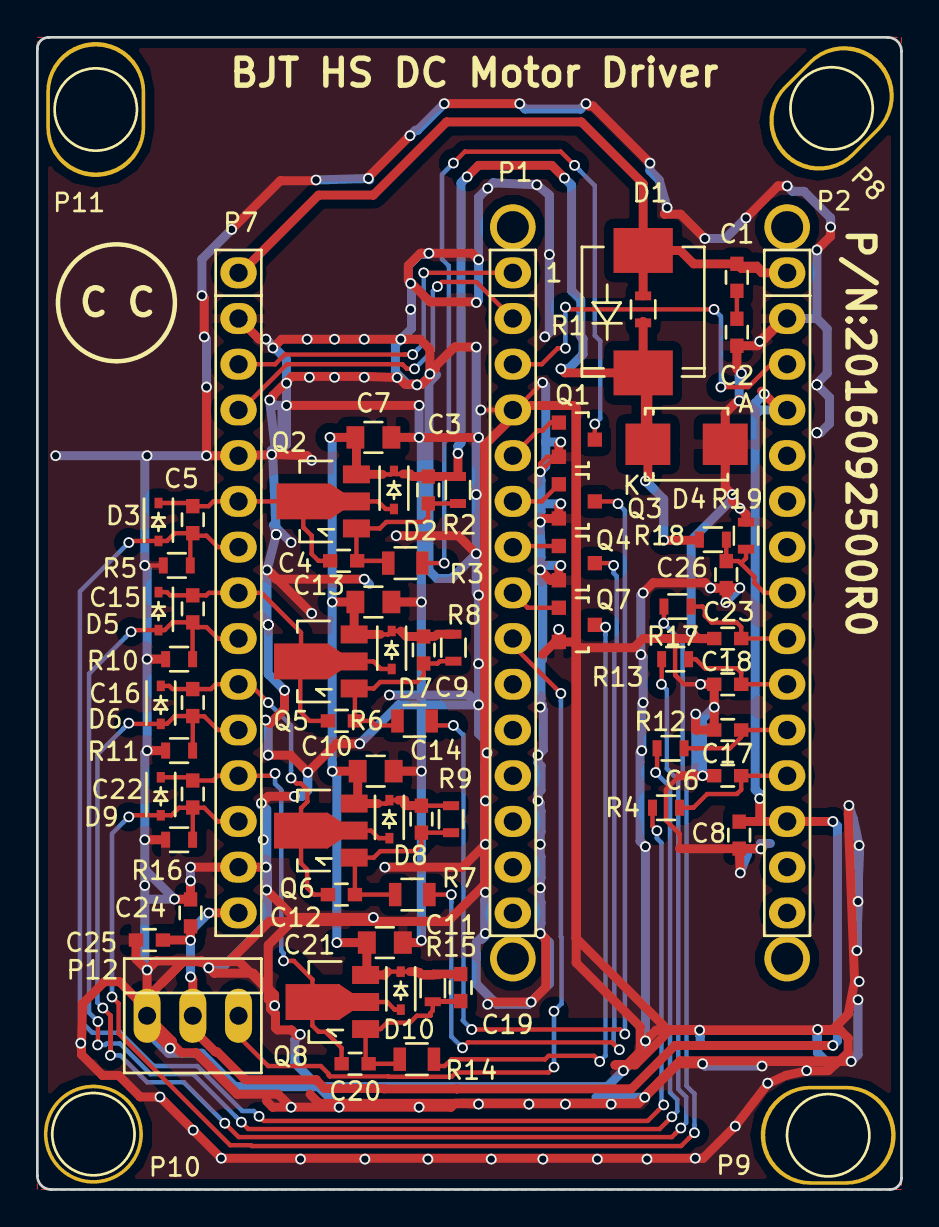
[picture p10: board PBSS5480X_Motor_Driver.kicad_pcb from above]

Board: 2 copper layers, 48.0 x 64.0 mm, 75 parts (0 on the bottom side), 34 nets.

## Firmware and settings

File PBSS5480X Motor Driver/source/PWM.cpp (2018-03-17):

#include 

class 4WhellPWM
{
public:
	int setPins( int pin1, int pin2, int pin3, int pin4 );
	int setDuty( unsigned short int PWMDuty1, unsigned short int PWMDuty2, unsigned short int PWMDuty3, unsigned short int PWMDuty4 );
	int getPWMPin1( void );
	int getPWMPin2( void );
	int getPWMPin3( void );
	int getPWMPin4( void );
	unsigned short int int getPWMDuty1( void );
	unsigned short int int getPWMDuty2( void );
	unsigned short int int getPWMDuty3( void );
	unsigned short int int getPWMDuty4( void );
	4WhellPWM ();
	~4WhellPWM();

private:
	int PWMpin1, PWMpin2, PWMpin3, PWMpin4;
	unsigned short int PWMDuty1, PWMDuty2, PWMDuty3, PWMDuty4;
	
	
};


// Functions Definition including the constructor and destructor
4WheelPWM::4WheelPWM(void)
{
	// Class initialization setting all PWMs to 0
	PWMpin1=PWMpin2=PWMpin3=PWMpin4=0;
	PWMDuty1=PWMDuty2=PWMDuty3=PWMDuty4=0;
	
	
}

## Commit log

2018-03-17 Initil Repository for PBSS5480x
    [PBSS5480X Motor Driver-B.Cu.gbr, PBSS5480X Motor Driver-B.Mask.gbr, PBSS5480X Motor Driver-B.SilkS.gbr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]
2019-01-16 Release 0.01
    First Release for Board Creation
    [PBSS5480X_Motor_Driver-B.Cu.gbr, PBSS5480X_Motor_Driver-B.Mask.gbr, PBSS5480X_Motor_Driver-B.SilkS.gbr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]
2019-01-16 Rev 0.02 Kicad 5.02 Conversion
    Convert Kicad 5.02 and Uploaded Schematic Diagram
    [PBSS5480X Motor Driver-2019-01-15-23-58-39.sch]
2019-01-27 Creating Documentation
    Continue Documentation adding board assembly information
    [PBSS5480X_Motor_Driver-2019-01-22-21-52-04.sch, PBSS5480X_Motor_Driver.kicad_pcb, PBSS5480X_Motor_Driver.sch]
2019-01-27 Block Diagram and License
    Added License information and Block Diagram
    [BlockDiagram.xlsx]
2019-01-27 Documentation update
    Added documentation Block Diagram png and Schematic diagram in png on docs
2019-01-27 Update README.md
    Added link to Schematic diagram png file
2019-01-27 Update README.md
    Added BOM
2019-01-27 Updates
    updated block diagram to show the battery monitor and power feed for motor drivers
    [BlockDiagram.xlsx, PBSS5480X_Motor_Driver.xlsx]
2019-02-17 Added Not Assembled Components
    The list of not assembled components was added by the results of the first assembled board
